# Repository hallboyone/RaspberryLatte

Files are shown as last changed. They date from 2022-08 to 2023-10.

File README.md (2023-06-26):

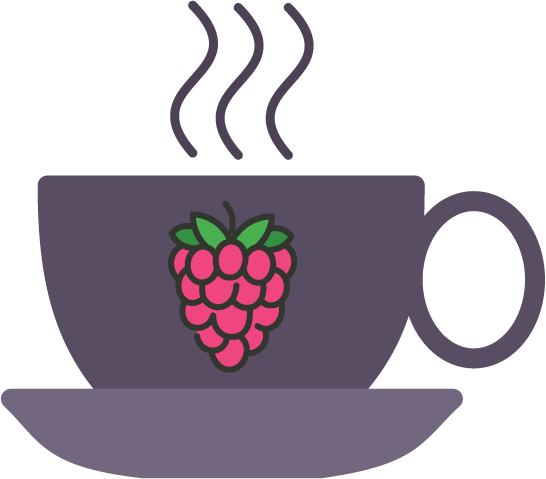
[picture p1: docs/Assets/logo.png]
#  RaspberryLatte 

A full stack suite to add smarts to a single boiler espresso machine using a Raspberry Pi Pico as the brains. The project was started with the following goals in mind:
- **Feature Rich:** Going beyond the standard PID temperature control, RaspberryLatte should provide advanced features that make pulling the perfect shot easier. These include
  - PID temperature control with feedforward components
  - Automatic flow control
  - Output scale
  - Preinfusion and autobrew routines
  - Coffee profiles
  - Scheduled heating *[Planned]*
  - Realtime state viewer (mobile UI) *[Planned]*
  - Machine statistic tracking *[Planned]*
  - Shot diagnosis and logging  *[Planned]*
- **Low Cost:** The cost should be minimized. The base hardware should be less than $100.
- **Discreet Appearance:** External parts, which would typically be 3D printed, should be minimized. Furthermore, the design should not require any external displays. In other words, the finished product should be discreet and not *look* like a DIY IoT device. 

## Features
### Advanced Temperature Control
Uses a PID controller with a feed-forward component to regulate the boiler's temperature. The resulting temperature is within 1% the setpoint throughout the shot.
<p align="center">
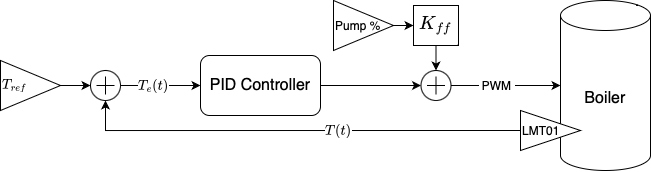
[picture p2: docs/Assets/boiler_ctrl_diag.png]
  
</p>

### Autobrew Routines with Flow Control
Automatically runs user configured brew routines. These will regulate the pump's power so that a desired flow rate is maintained over the course of the shot.

<p align="center">
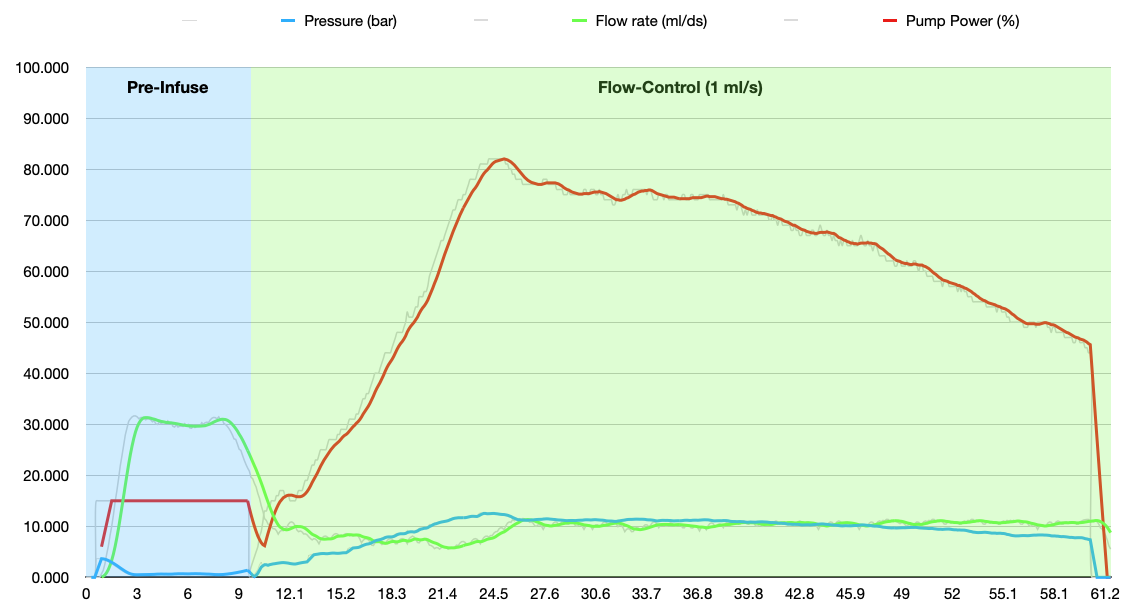
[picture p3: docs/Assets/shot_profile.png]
  
</p>

### User Adjustable Settings
The temperatures, flow rate, preinfusion routine, dose, yield, and other settings can all be customized without reflashing the code. The pump switch and mode dial are used to navigate a folder structure while the three LEDs display the current values of the parameters as they are adjusted. This allowed for full customization without any additional hardware (e.g. screens, buttons, etc.). 

## Project Architecture 

This project can be thought of in several layers. 
### Hardware Level
The lowest level is the hardware such as sensors and switches required to create a smart espresso machine. Additionally, a custom carrier board is needed to interface with these components. This PCB contains any circuitry required to support the sensors and switches. Mounted to this carrier board is the Raspberry Pi Pico W.
| Front View | Back View |
| --- | --- |
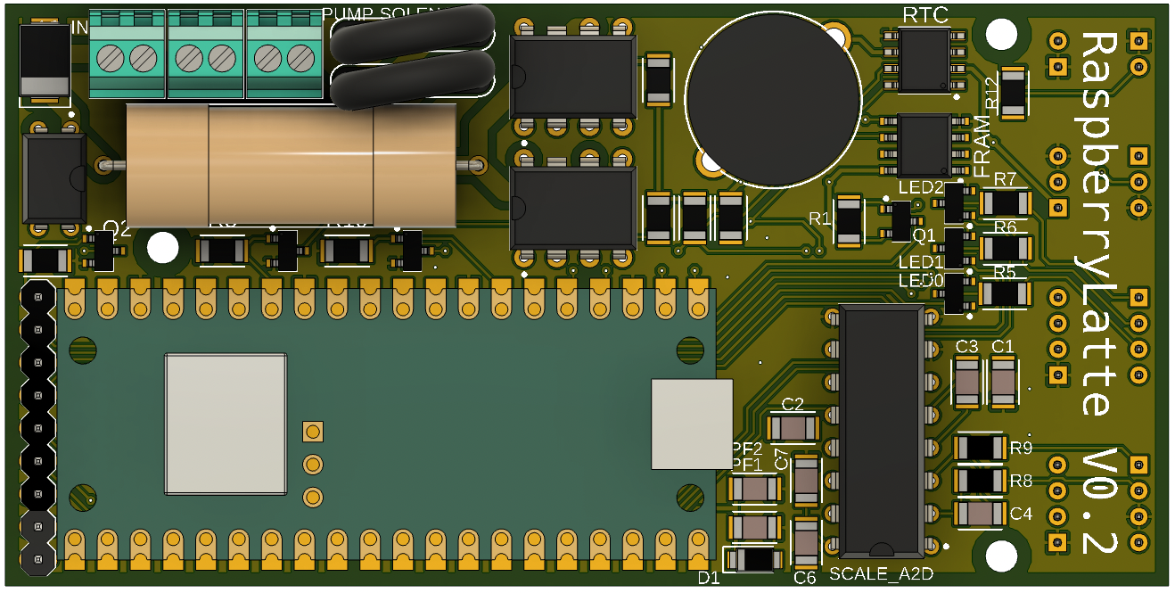
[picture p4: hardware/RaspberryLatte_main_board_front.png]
Front view of main board
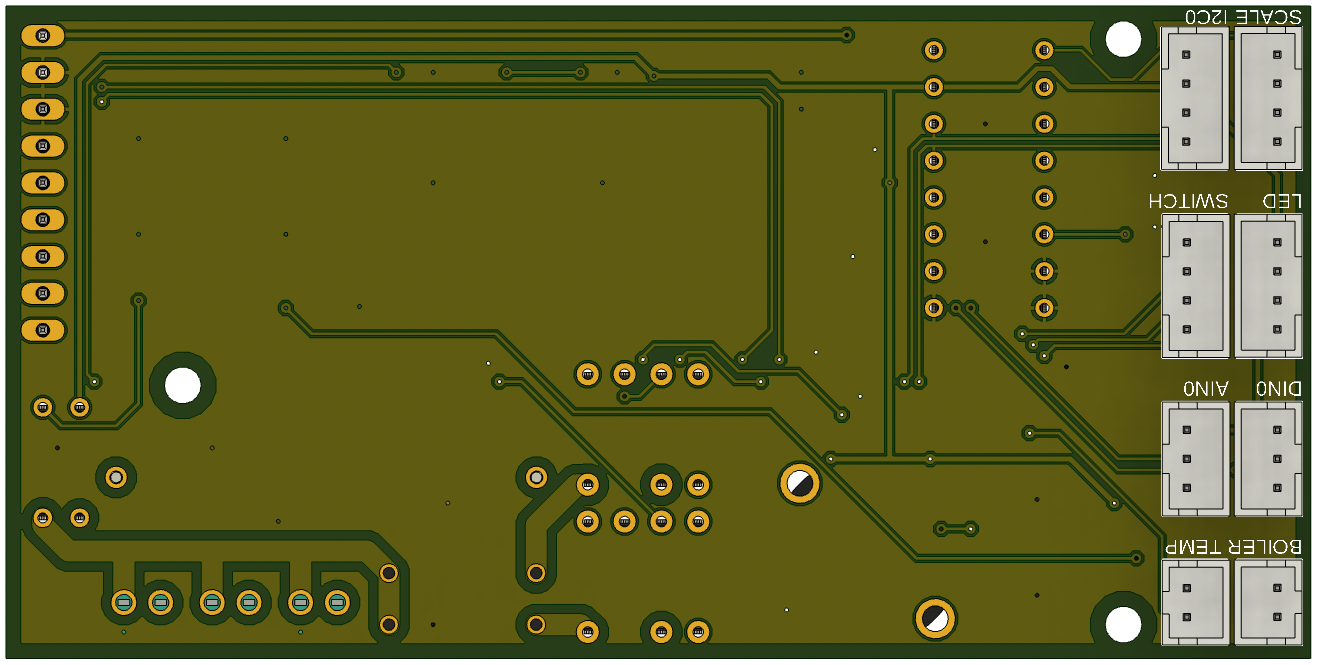
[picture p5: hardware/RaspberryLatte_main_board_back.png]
Back view of main board
 | 

### Firmware Level
The next level consists of the firmware running on the Pico. This code, written in c, contains all the sensor drivers and machine logic. The firmware is partitioned onto a single core of the dual core Pico.
### Network Level (Planned)
The network level runs on the second core on the Pico. It collects information from the firmware running on core 0 and shares that over BLE with the Mobile UI level (see below). It also passes settings received from a BLE client to the firmware so that the machines performance can be tailored to achieve the desired brew characteristics.
### Mobile UI Level (Planned)
While ssh is fun, a mobile application would be significantly more convenient. This level would allow users to create and share their brew profiles for different coffees, visualize a shot's flow rate, pressure, temperature, etc. in real time, and troubleshoot their shots. This application would interface with the Network level using BLE, simplifying the connection process.

## To-Do
- [x] Add carrier board design to repository
- [x] Add UI based on onboard switches and LEDs
- [x] Add flow control to autobrew routines
- [ ] Add wiring diagram
- [ ] Add BOM for hardware
- [ ] Implement network leve
- [ ] Implement mobile UI level
- [x] Design logo
- [ ] Write project documentation

## Documentation
### Project Documentation (Under Construction)
To help with your build, project documentation is being written in another [repository](https://github.com/hallboyone/RaspberryLatte-docs). Clone and build the sphinx docs to view.
<p align="center">
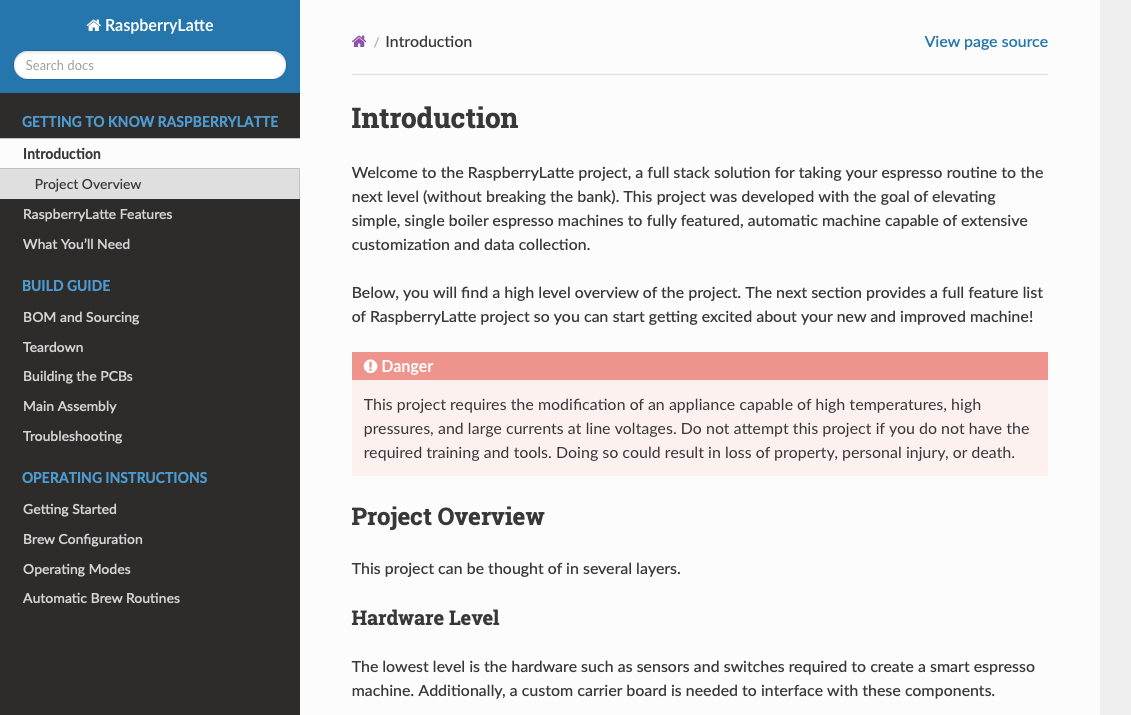
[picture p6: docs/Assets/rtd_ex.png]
RTD Documentation screenshot
  
</p>

### Code Documentation
The documentation is generated from the code's comments using doxygen. Below is a sample page showing the autobrew library. Clone and build the html to view the rest.
<p align="center">
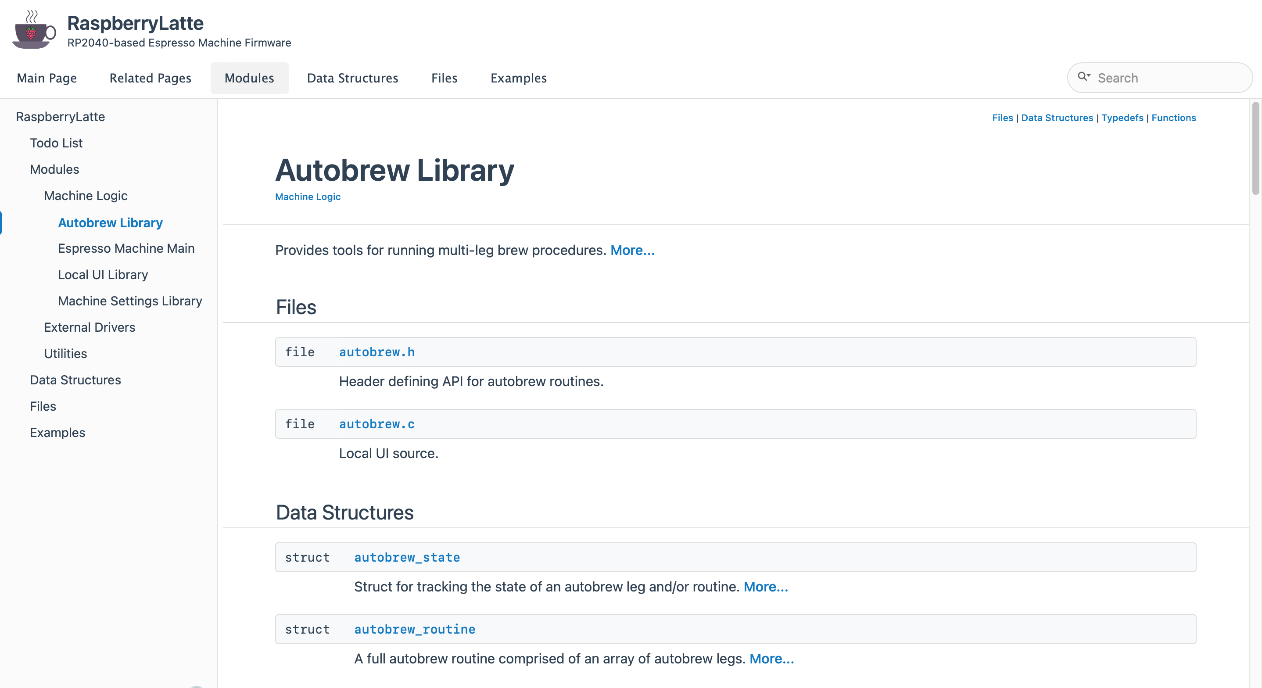
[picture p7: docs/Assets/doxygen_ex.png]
Doxygen screenshot
  
</p>

## Inspiration
This project has taken inspiration from others who have taken the time to write up their own builds. The two primary sources have been the [Es(pi)resso project](https://home-automations.net/project-coffee-espiresso-machine/), and the [Espresso for Geeks blog](https://www.instructables.com/Espresso-for-Geeks/). Big thank you to both those makers for sharing the great work they did!

## Contribute
If you are interested in helping with this project, I would love to talk! You can reach me through [Twitter](https://twitter.com/hallboyone "Richard Hall").

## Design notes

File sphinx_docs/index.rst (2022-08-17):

.. RaspberryLatte documentation master file, created by
   sphinx-quickstart on Tue Aug 16 21:35:44 2022.
   You can adapt this file completely to your liking, but it should at least
   contain the root `toctree` directive.

Welcome to RaspberryLatte's documentation!
==========================================

.. toctree::
   :maxdepth: 2
   :caption: Contents:

Indices and tables
==================

* :ref:`genindex`
* :ref:`modindex`
* :ref:`search`

Docs
====
.. doxygenfile:: autobrew.h

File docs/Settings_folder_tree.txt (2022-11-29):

0. Root (ooo)
    0.1. Settings (oox)
        0.1.1 Temp (oxo)
            0.1.1.1 Brew  [-1, 0.1, 1]
            0.1.1.2 Hot   [-1, 0.1, 1]
            0.1.1.3 Steam [-1, 0.1, 1]
        0.1.2 Weight (oxx)
            0.1.2.1 Dose  [-1, 0.1, 1]
            0.1.2.2 Yield [-1, 0.1, 1]
        0.1.3 More (xoo)
            0.1.3.1 Power (xox)
                0.1.2.1.1 Brew [-10, 1, 10]
                0.1.2.1.2 Hot  [-10, 1, 10]
            0.1.3.2 Preinf (xxo)
                0.1.3.2.1 On time  [-1, 0.1, 1]
                0.1.3.2.2 On power [-10, 1, 10]
                0.1.3.2.3 Off time [-1, 0.1, 1]
            0.1.3.3 Misc (xxx)
                0.1.3.3.1 Timeout   [-10, 1, 10]
                0.1.3.3.2 Ramp time [-1, 0.1, 1]
    0.2 Profiles (oxo)
        0.2.1 Profiles 1-3 (oxx)
            0.2.1.1 Profile 1 (xoo) [Save, Load, ~]
            0.2.1.2 Profile 2 (xox) [Save, Load, ~]
            0.2.1.3 Profile 3 (xxo) [Save, Load, ~]
        0.2.2 Profile 4-6 (xoo)
            0.2.2.1 xox Profile 4 (xox) [Save, Load, ~]
            0.2.2.2 xxo Profile 5 (xxo) [Save, Load, ~]
            0.2.2.3 xxx Profile 6 (xxx) [Save, Load, ~]
        0.2.3 Profile 7-9 (xox)
            0.2.3.1 xxo Profile 7 (xxo) [Save, Load, ~]
            0.2.3.2 xxx Profile 8 (xxx) [Save, Load, ~]
            0.2.3.3 ooo Profile 9 (ooo) [Save, Load, ~]

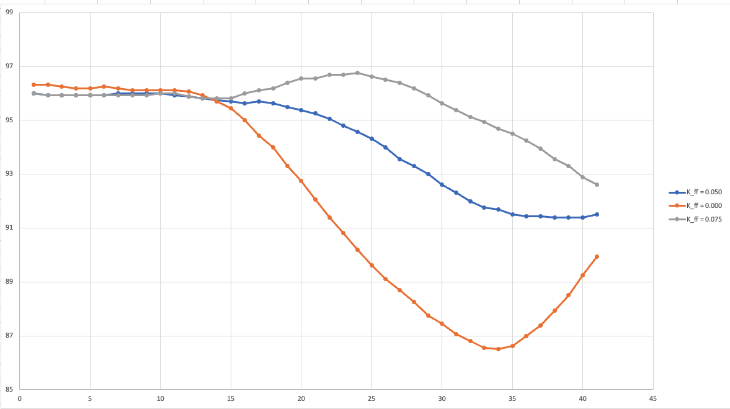
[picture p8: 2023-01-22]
docs/ff_comparison.png

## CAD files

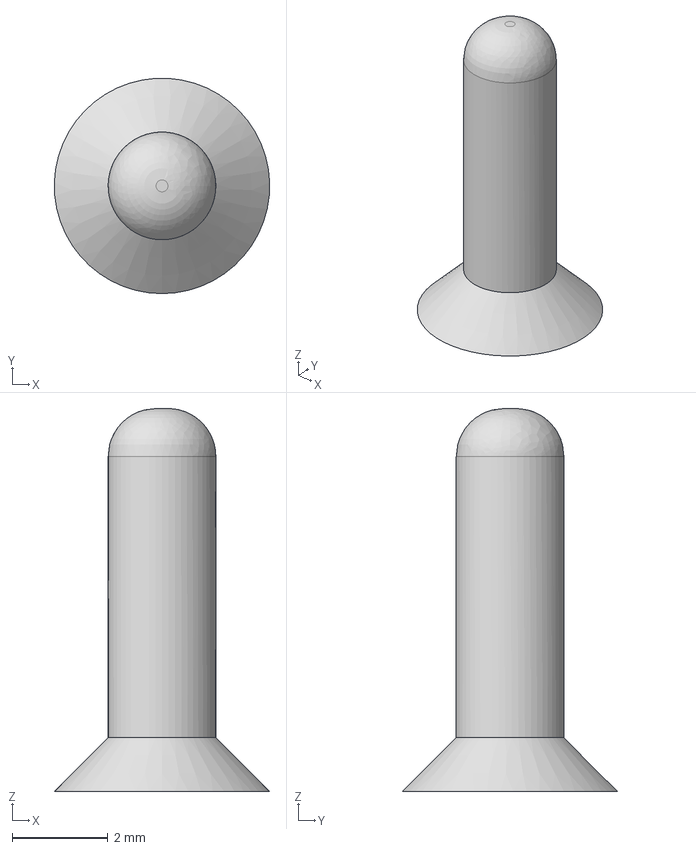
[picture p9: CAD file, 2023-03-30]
hardware/solid_models/main_board_pin.step
4.50 x 4.50 x 8.00 mm

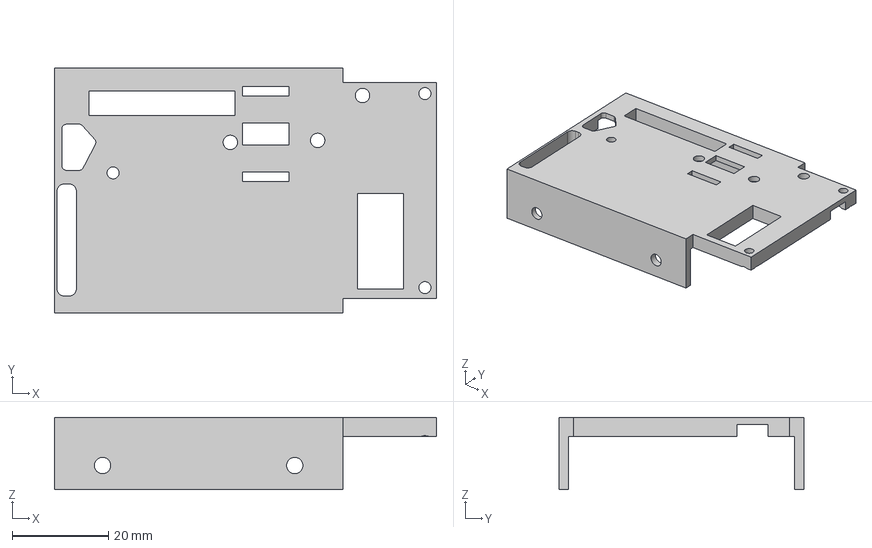
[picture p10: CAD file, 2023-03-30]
hardware/solid_models/main_board_mount.step
79.5 x 51.0 x 15.0 mm

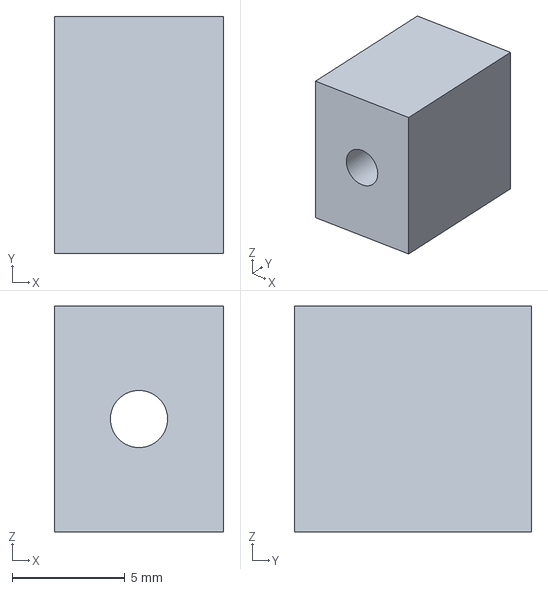
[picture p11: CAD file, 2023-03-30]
hardware/solid_models/led_board_mount.step
7.50 x 10.5 x 10.0 mm

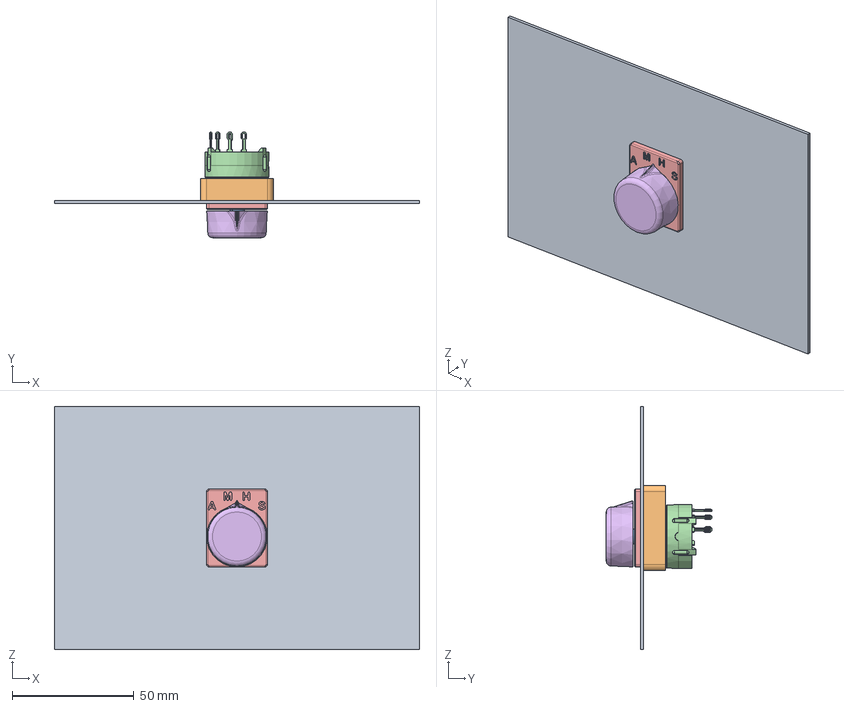
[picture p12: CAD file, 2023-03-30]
hardware/solid_models/mode_dial.step
150.0 x 43.4 x 100.0 mm
Switch_face
Clamp_back
Clamp_front
Knob

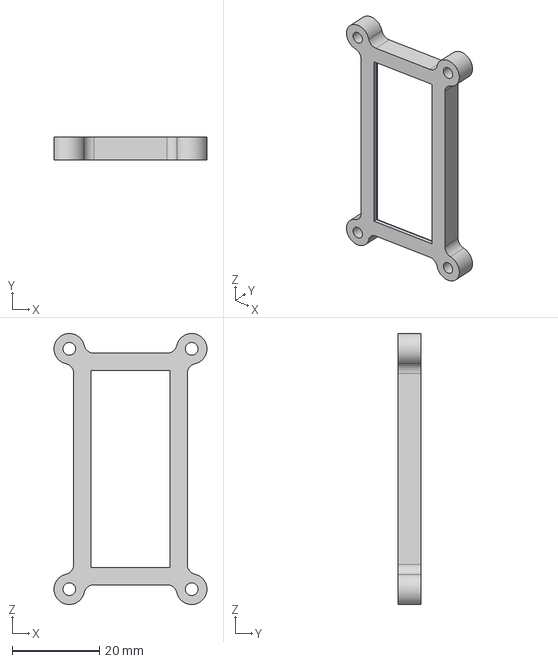
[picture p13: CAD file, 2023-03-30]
hardware/solid_models/power_supply_mount.step
35.0 x 5.25 x 62.0 mm

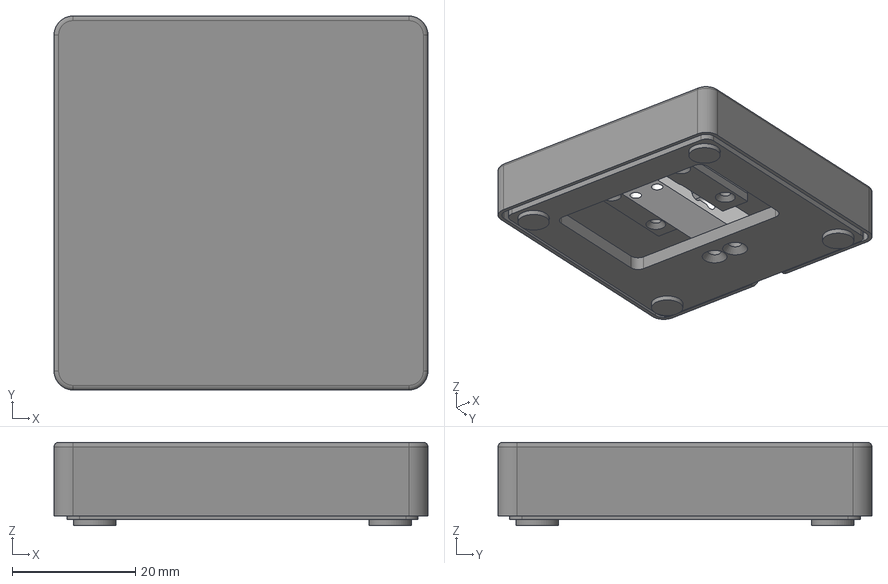
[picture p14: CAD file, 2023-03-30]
hardware/solid_models/espresso_scale.step
60.7 x 60.7 x 13.6 mm
Load cell
scale_base
scale_top_mount
scale_top
foot x 4

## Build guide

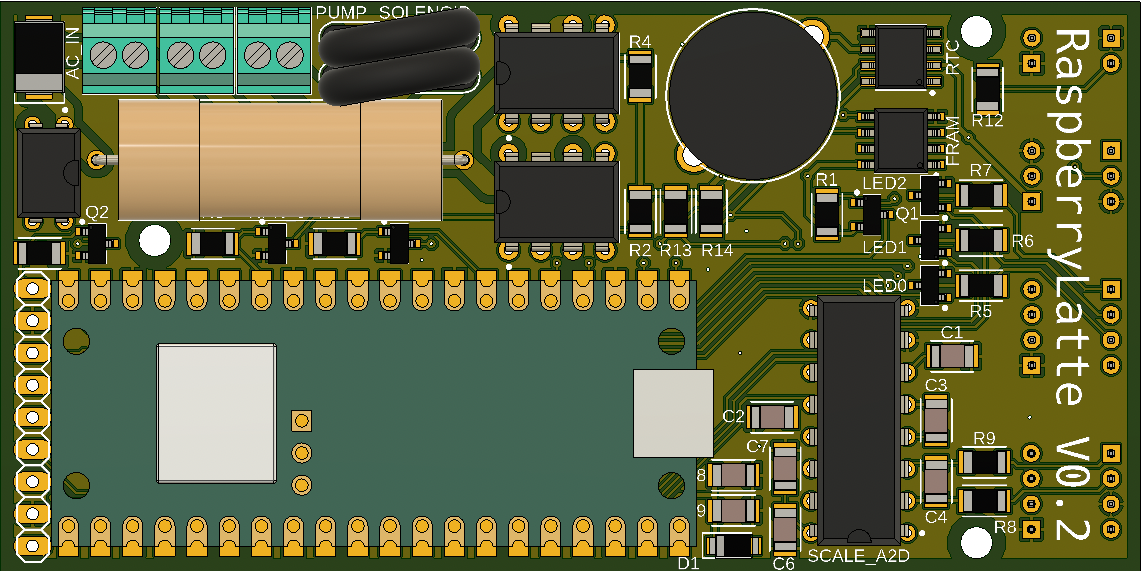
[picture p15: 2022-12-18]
docs/Wiring_diagram/main_board.png

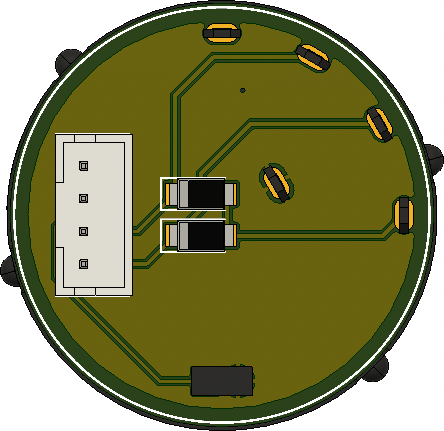
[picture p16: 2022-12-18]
docs/Wiring_diagram/dial_board.png

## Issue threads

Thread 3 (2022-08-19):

Missing I2C pull up resisters

hallboyone, 2022-08-19:
## Problem Summary
There is a note in section 4.3.1.3 of the RP2040 data sheet discussing the use of the RP2040's I2C hardware. It reads
> Note: There should also be external pull-ups on the board as the internal pad pull-ups may not be strong enough to pull up external circuits.

However, the current schematic relies on the internal pull-ups. This could be the cause of the intermittent problems communicating with the NAU7802.

## Proposed Solution
Add 4.7KOhm pull up resisters to the SDA and SCL lines on the RaspberryLatte main board.

hallboyone, 2022-10-05:
Fixed with new version of main board

Closed 2022-10-05.

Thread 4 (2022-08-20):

No external pull-up/pull-down resisters on board

hallboyone, 2022-08-20:
## Problem Summary
There are no external pull resisters on any of the main board's output signals (include the I2C bus as stated in #3). This can lead to dangerous situations where a crashed program and floating output can cause one of the AC components (heater, pump, solenoid) to get stuck in the on position.

## Proposed Solution
Add 4.7KΩ pull up resisters to all the output signal lines on the RaspberryLatte main board.

hallboyone, 2022-10-05:
Fixed with new version of main board

Closed 2022-10-05.

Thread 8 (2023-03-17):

Flow rate starts at non-zero value when machine is switched on.

hallboyone, 2023-03-17:
Probably something is not being reset correctly.

hallboyone, 2023-03-18:
After a little testing, the problem has been traced to noise in the flow sensor's power supply when the machine is switched on. This is read as a pulse by the pico. I tried a software fix (zeroing the flow sensor when the machine is powered on), but this led to corner cases where the sensor would be zeroed and then pulsed, leading to an occasional very large spike. It will be best to just clean the 5V power in the next version of the PCB. Until then, there will be some phantom flow rate now and then when the machine is turned on.

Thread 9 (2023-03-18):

Ground plan around AC traces

hallboyone, 2023-03-18:
There is not enough clearance around the traces caring AC loads on the PCB. The ground plan should be carved out in this area.

hallboyone, 2023-05-05:
Working on next version of PCB that fixes this.
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

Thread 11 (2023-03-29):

5V flow rate not supported by control board without modifications

hallboyone, 2023-03-29:
The control board was designed for 3.3V flow sensors. Turns out, they are almost exclusively 5V. To get around this with the current design, a jumper has to be soldered on and a voltage divider used to drop the 5V signal down to 3V. This should be updated in the next version of the board so no jumpers are needed. This is also related to issue #8 discussing cleaning the power to the flow sensor.

hallboyone, 2023-05-05:
I'm working on an update for the PCB that addresses this.
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

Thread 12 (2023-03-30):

Make integral windup bound dependent on output limits.

hallboyone, 2023-03-30:
Currently, the integral windup bound is set to a fixed value. However, this can lead to overshoot e.g. during flow control when 100% power is needed to reach the target flow rate. This leads to `e(t)*Kp + e_sum(t)*Ki = e(t)*Kp + 100 > 100` (where the last inequality holds only when the flow is below the target).

 Instead of the fixed bounds, `e_sum_lb <= e_sum(t) <= e_sum_ub`, the windup bound on the integral term should dependent on the proportional  input: `e_sum_lb - e(t)Kp <= e_sum(t) <= e_sum_ub - e(t)*Kp`. This is equivalent to the fixed bounds when at the set point, but it keeps prevents the error sum from growing when the error is large (i.e. the proportion term is dominate).

Closed 2023-03-30.

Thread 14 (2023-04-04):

Add pressure profiling to autobrew routines

hallboyone, 2023-04-04:
Currently, the auto brew routine can only regulate the flow rate. It is possible that the user may want to regulate the pressure instead. This should be added as an option for the auto brew routine.

Closed 2023-07-03.

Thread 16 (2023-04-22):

CRITICAL - Occasional erratic behavior in boiler

hallboyone, 2023-04-22:
I have observed occasional erratic behavior in the boiler. I'm not sure if it's software (sensor driver, PID implementation, etc) or hardware (sensor failure). Best guess is an overflow error somewhere in the PID controller, but I need to do more tests.

hallboyone, 2023-04-23:
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
After some testing, I think the problem is with the LMT01 sensor. For a single reading, the sensor will begin to report a temp around -50C, and the controller responds as it should. If these misreadings happen with increased frequency, the temperature will begin to increase and display the behavior I have observed.

Regardless of why we are getting bad readings, additional safe guards are needed to catch and stop this failure. Perhaps an error triggered by large differences between two temp readings. This should disable the boiler at the very least.

hallboyone, 2023-04-26:
While the sensor bug should definitely be addressed at some point, I think more important is the development of a boiler malfunction monitor within the code. I'll be opening a new issue to address it.

hallboyone, 2023-06-20:
After further thought, I think a median filter should be applied to the LMT01 sensor. This will reject the periodic spikes in its readings. The thermal runaway is triggered to throw an error if the temp reading varies too quickly so a spike will trip it (even if behavior returns to normal at the next reading). A median filter should fix this while only delaying the detection of a true problem by a couple hundred ms at most.

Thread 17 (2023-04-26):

Add thermal runaway safeguards

hallboyone, 2023-04-26:
There is currently nothing checking that the boiler is responding as expected to the heater inputs. This can lead to thermal runaways should the sensor come detached or fail. Functionality should be added to monitor the state of the boiler and enter an error state should a thermal runaway be sensed.
This could be modeled after the thermal runaway logic in the Marlin 3D printer firmware. The basic rules are
1.  The temp must be changing at some minimum rate when the machine is settling to a temperature (i.e. responding to control inputs)
2. The temp must not deviate too far from the setpoint after settling (i.e. sensor fails as in #16)

Closed 2023-05-04.

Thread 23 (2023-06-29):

Replace return-to-root with up-a-level in local_ui

hallboyone, 2023-06-29:
Currently, once you are don't changing a setting using the local_ui, you have to return to root before changing another setting. This is very annoying and would be better replaced with just going up a single level to the parent folder.

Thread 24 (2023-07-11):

ENHANCEMENT-update-settings-in-terminal

hallboyone, 2023-07-11:
Using the local dial and pump switch, though functional, is very clunky. With the newly expanded setting structure (120 folders!) it takes a long time to navigate and get set the way you want it. It would be much easier to do this with a console interface prior to the implementation of a remote application.

hallboyone, 2023-07-11:
This ended up being a bigger project than the original scope. The settings are now displayed as
```
Brew Temp   :  92.0 C
Hot Temp    : 100.0 C
Steam Temp  : 140.0 C
Dose        :  16.0 g
Yield       :  30.0 g
Brew Power  :   100 %
Hot Power   :    20 %

|=|=========================|========================|=========|
| |        Setpoint         |         Target         | Timeout |
|#|  Style  : Start :  End  | Flow : Pressure : Mass |         |
|-|---------:-------:-------|------:----------:------|---------|
|0|  Power  :   100 :   100 | 0.50 :    1.0   : 10.0 |  30.0   |
|1|  Flow   :  0.25 :  0.25 | 0.00 :    0.0   :  0.0 |   0.0   |
|2| Pressure:   2.5 :   2.5 | 0.00 :    0.0   :  0.0 |   0.0   |
|3|  Power  :    25 :    25 | 0.00 :    0.0   :  0.0 |   0.0   |
|4|  Power  :    25 :    25 | 0.00 :    0.0   :  0.0 |   0.0   |
|5|  Power  :    25 :    25 | 0.00 :    0.0   :  0.0 |   0.0   |
|6|  Power  :    25 :    25 | 0.00 :    0.0   :  0.0 |   0.0   |
|7|  Power  :    25 :    25 | 0.00 :    0.0   :  0.0 |   0.0   |
|8|  Power  :    25 :    25 | 0.00 :    0.0   :  0.0 |   0.0   |
|=|=========================|========================|=========|

RaspberryLatte
 (1) Settings
 (2) Autobrew
 (3) Presets
```
This is much cleaner than it was and should maintain it's format during use without needing to reprint everything with each change.

The settings can be navigated while the machine is off using "1"-"3" for subfolder selection, "u" to go up a level, "r" to go to root, and "p" to reprint (e.g. after resizing the terminal window).

Closed 2023-07-11.

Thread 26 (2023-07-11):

Flow rate sensor is slow and not accurate at low flows

hallboyone, 2023-07-11:
It could be replaced with something like [this](https://www.alibaba.com/product-detail/EPT-small-size-output-water-flow_1600425267625.html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). However, this will require retuning everything, but this is probably okay since the flow control never worked great anyway.

hallboyone, 2023-07-12:
I'm testing a new sensor (linked above) and have collected the following data.
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
The slope of the trend line is the conversion between the pulses and volume. The exact values to 6 decimal places are
```
slope     =  0.009472
intercept = -0.054317
```

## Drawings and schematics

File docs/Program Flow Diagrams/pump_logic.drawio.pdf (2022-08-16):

## Espresso Machine Pump Logic

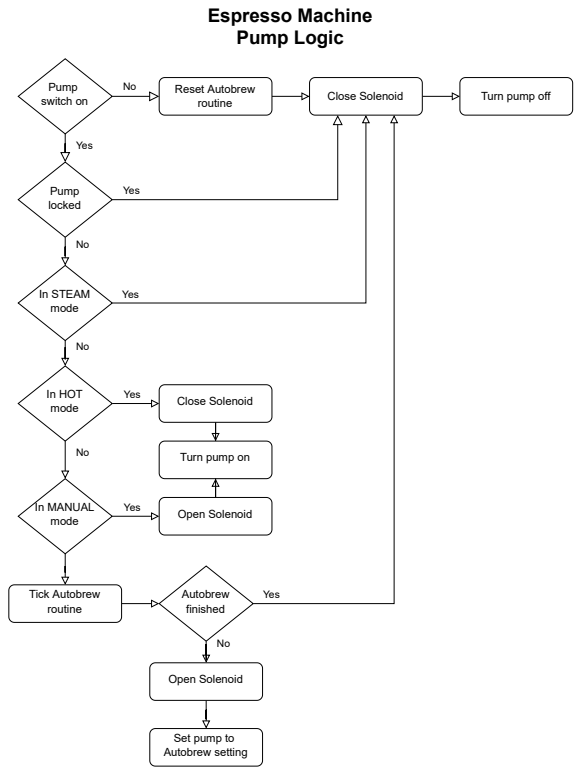
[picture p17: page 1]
Yes; Pump; switch on; Reset Autobrew routine; Pump locked; Close Solenoid; Turn pump off; In STEAM mode; In HOT; mode; In MANUAL; Open Solenoid; Tick Autobrew routine; Autobrew; finished

Turn pump on

Set pump to
Autobrew setting

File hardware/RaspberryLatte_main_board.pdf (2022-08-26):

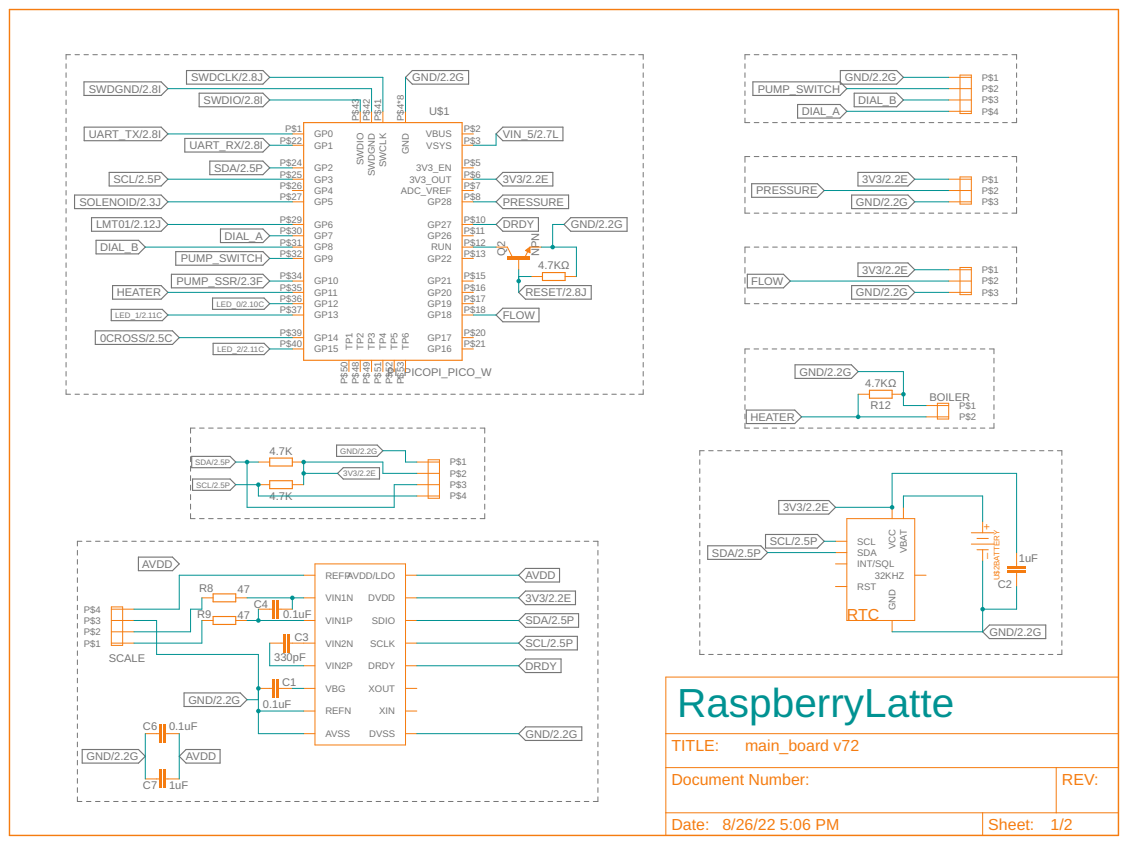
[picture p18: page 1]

Document Number: | REV:

Date: 8/26/22 5:06 PM | Sheet: 1/2

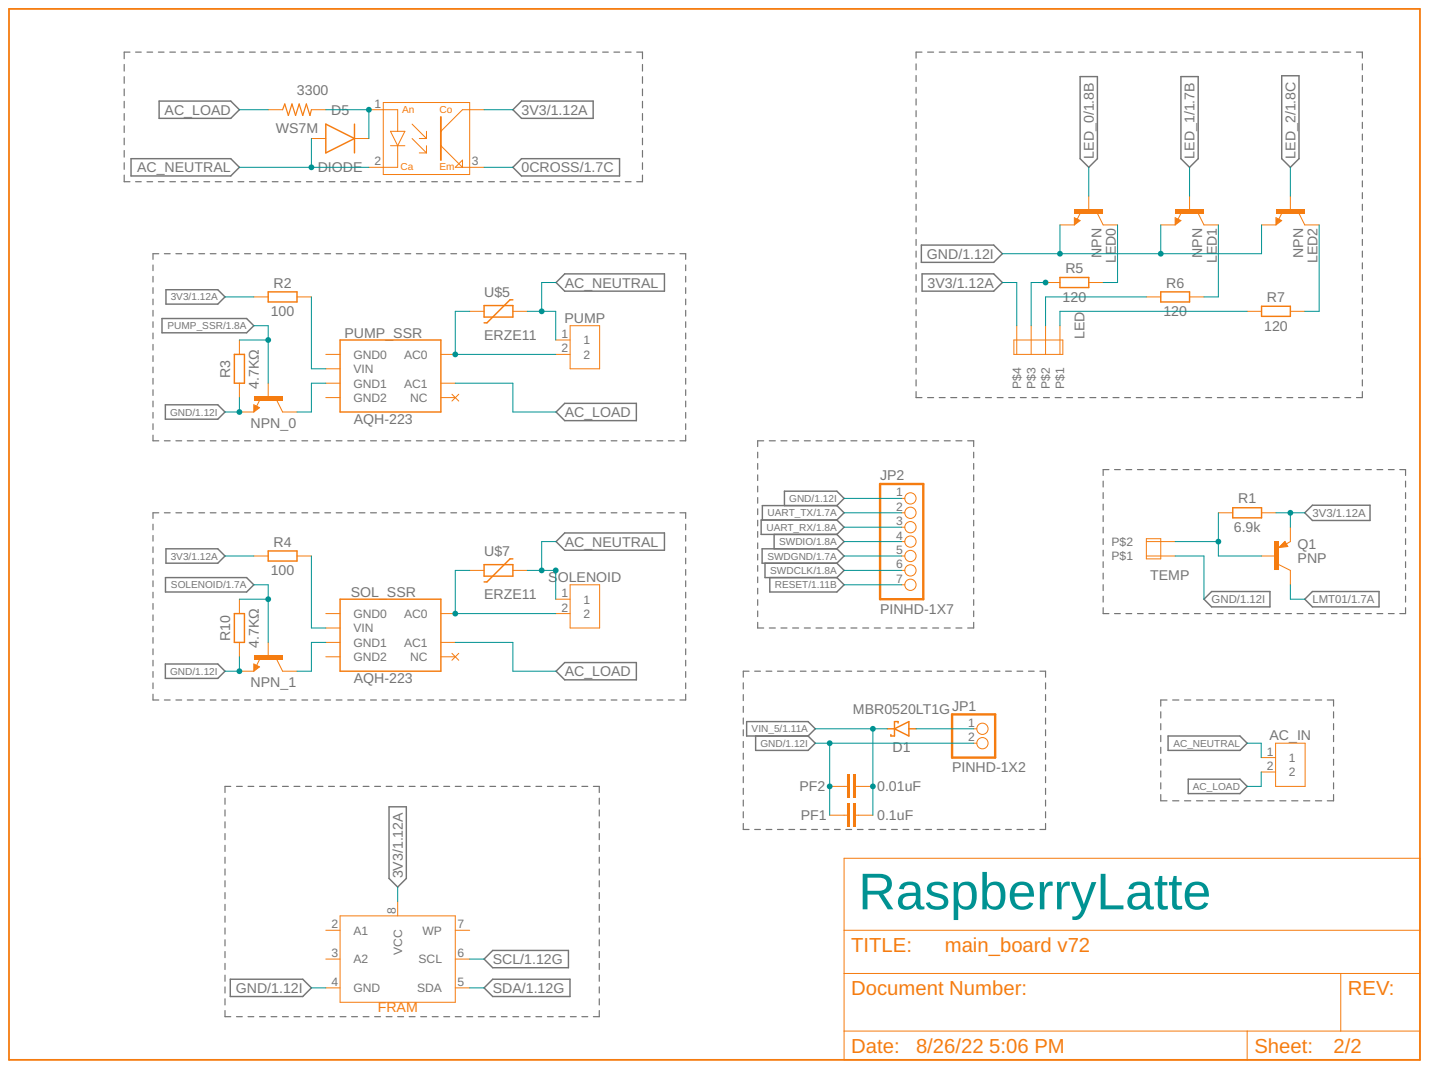
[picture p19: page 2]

Document Number: | REV:

Date: 8/26/22 5:06 PM | Sheet: 2/2

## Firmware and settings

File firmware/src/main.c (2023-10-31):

#define PRINT_MACHINE_STATUS_OVER_UART

#ifdef PRINT_MACHINE_STATUS_OVER_UART
#include <stdio.h>
#endif

#include "machine_logic/espresso_machine.h"

int main(){
    // Setup UART
    stdio_uart_init_full(PICO_DEFAULT_UART_INSTANCE, 115200, PICO_DEFAULT_UART_TX_PIN, PICO_DEFAULT_UART_RX_PIN);

    espresso_machine_viewer espresso_machine;
    if(espresso_machine_setup(&espresso_machine)) return 1;

    // Loop rate limiter
    absolute_time_t next_loop_time = get_absolute_time();
    const uint64_t loop_period_ms = 10;

    #ifdef PRINT_MACHINE_STATUS_OVER_UART
    const uint16_t ticks_per_message = 20;
    uint32_t num_ticks = 0;
    #endif

    while(true){
        next_loop_time = delayed_by_ms(next_loop_time, loop_period_ms);

        #ifdef PRINT_MACHINE_STATUS_OVER_UART
        num_ticks += 1;
        // Print status periodically 
        if(num_ticks%ticks_per_message == 0){
            if(espresso_machine->switches.ac_switch){
                printf("%5.1f\t%5.1f\t%3d\t%2d\t%3d\t%5.2f\t%4.1f\t%d\n",
                espresso_machine->boiler.setpoint/100.,
                espresso_machine->boiler.temperature/100.,
                espresso_machine->boiler.power_level,
                espresso_machine->autobrew_leg,
                espresso_machine->pump.power_level,
                espresso_machine->pump.flowrate_ml_s,
                espresso_machine->pump.pressure_bar,
                espresso_machine->scale.val_mg);
            }
        }
        #endif

        // Update the machine
        espresso_machine_tick();

        sleep_until(next_loop_time);
    }
}

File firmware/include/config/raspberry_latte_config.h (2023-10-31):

/**
 * Length of time after powering on that the boiler and pump remain inactive. 
 * Let's transient voltages settle out before activating the machine.
 */
#define AC_SETTLING_TIME_MS 500

/** \brief The difference between the zerocross sense time and the actual zerocross time. */
#define AC_0CROSS_SHIFT 0

#define BOILER_PID_GAIN_P 0.05
#define BOILER_PID_GAIN_I 0.00000175
#define BOILER_PID_GAIN_D 0.0
#define BOILER_PID_GAIN_F 0.00005
#define FLOW_PID_GAIN_P   0.0125
#define FLOW_PID_GAIN_I   0.00004
#define FLOW_PID_GAIN_D   0.0
#define FLOW_PID_GAIN_F   0.0

#define SCALE_CONVERSION_MG -0.152710615479

/** ml per pulse of pump flow sensor. */
#define PULSE_TO_FLOW_CONVERSION_ML  0.009472

// Between two temp readings, the temperature must not change by more than this amount.
#define THERMAL_RUNAWAY_WATCHER_MAX_CONSECUTIVE_TEMP_CHANGE_cC 1000

// Defines the window over which a change in temperature must be observed while converging to setpoint.
#define THERMAL_RUNAWAY_WATCHER_MIN_TEMP_CHANGE_PERIOD_MS 20000
#define THERMAL_RUNAWAY_WATCHER_MIN_TEMP_CHANGE_HEAT_cC  200
#define THERMAL_RUNAWAY_WATCHER_MIN_TEMP_CHANGE_COOL_cC  100

// Defines how close to the setpoint counts as convergence and how far counts as divergence
#define THERMAL_RUNAWAY_WATCHER_CONVERGENCE_TOL_cC 100
#define THERMAL_RUNAWAY_WATCHER_DIVERGENCE_TOL_cC  800

#define PUMP_SWITCH_DEBOUNCE_DURATION_US 10000
#define MODE_DIAL_DEBOUNCE_DURATION_US 75000

#define AUTOBREW_PREINF_END_PRESSURE_MBAR 3000
#define AUTOBREW_BREW_PRESSURE_MBAR       9000

#define THERMAL_RUNAWAY_WATCHER_LED_TOGGLE_PERIOD_MS 512

/**
 * The temp that the thermometer is reading may not match the water at the group-head.
 * This constant defines the discrepancy. Compute the value in C and then multiply by 
 * 16 and round to an integer. 
*/
#define BOILER_TEMP_OFFSET_cC 800

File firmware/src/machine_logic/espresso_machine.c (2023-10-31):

/**
 * \file espresso_machine.c
 * \ingroup espresso_machine
 * \author Richard Hall (hallboyone@icloud.com)
 * \brief Espresso Machine source
 * \version 0.1
 * \date 2022-12-09
 */

//#define ENABLE_BOILER

#include "machine_logic/espresso_machine.h"

#include <stdio.h>

#include "config/raspberry_latte_config.h"
#include "config/pinout.h"

#include "machine_logic/autobrew.h"
#include "machine_logic/machine_settings.h"

#include "drivers/nau7802.h"
#include "drivers/lmt01.h"
#include "drivers/ulka_pump.h"

#include "utils/thermal_runaway_watcher.h"
#include "utils/gpio_irq_timestamp.h"
#include "utils/binary_output.h"
#include "utils/binary_input.h"
#include "utils/slow_pwm.h"
#include "utils/i2c_bus.h"
#include "utils/pid.h"
#include "utils/macros.h"

/** An internal variable that collects the current state of the machine. */
static espresso_machine_state _state = {.pump.pump_lock = true, .boiler.temperature = 0}; 

/** I2C bus connected to memory, scale ADC, and I2C port */
static i2c_inst_t *  bus = i2c1;
static thermal_runaway_watcher trw;         /**< Watches the boiler state to make sure it's behaving as expected. */
static binary_output           leds;        /**< The three LEDs indicating to the user the machine's state. */
static binary_input            pump_switch; /**< Monitors the state of the pump switch. */
static binary_input            mode_dial;   /**< Monitors the state of the mode dial. */
static absolute_time_t         ac_on_time;  /**< Records the time of when the machine was switched on. */
static binary_output           solenoid;    /**< Drives the digital output for the solenoid. */
static slow_pwm                heater;      /**< PWM signal for the SSR driving the boiler. */
static lmt01                   thermo;      /**< Boiler thermometer. */
static nau7802                 scale;       /**< Output scale. */
static ulka_pump               pump;        /**< The vibratory pump. */

/** Boiler controller */
static pid  heater_pid;
/** Flow controller */
static pid  flow_pid;                    

#ifdef ENABLE_BOILER
/** 
 * \brief Shuts down the pump and boiler. 
*/
static void espresso_machine_e_stop();
#endif

/**
 * \brief Checks if the AC is on.
 * If the last AC zerocross time was within 17,000us (a little over a 60hz 
 * period), then it's assumed on.
 * \return True AC is on. False otherwise.
 */
static inline bool is_ac_on(){
    return (gpio_irq_timestamp_read_duration_us(AC_0CROSS_PIN) < 17000);
}

/** 
 * \brief Checks if AC has settled.
 * The AC is assumed settled once AC_SETTLING_TIME_MS have passed and AC is on. 
 * The time should be long enough to allow transient spikes to die out. 
 * \return True if ac has settled. Else, returns false.
 */
static inline bool is_ac_on_and_settled(){
    return is_ac_on() && absolute_time_diff_us(ac_on_time, get_absolute_time()) > 1000*AC_SETTLING_TIME_MS;
}

/** 
 * \brief Getter for the boiler temp. 
 * Used as a helper function for the boiler PID controller.
 * \returns The current boiler temp in C. 
 */
static pid_data read_boiler_thermo_C(){
    return lmt01_read_float(thermo);
}

/** 
 * \brief Getter for the pump's flowrate. 
 * Used as a helper function for the pumps flow controller.
 * \returns The current flow rate through the pump in ul/s. 
 */
static pid_data read_pump_flowrate_ul_s(){
    return 1000.0*ulka_pump_get_flow_ml_s(pump);
}

/** 
 * \brief Setter for the boiler's duty cycle. 
 * Used as a helper function for the boiler PID controller.
 * \param u A duty cycle with 0 being off and 1 being full on.
 */
static void apply_boiler_input(float u){
    slow_pwm_set_float_duty(heater, u);
}

/** 
 * \brief Zeros the scale. 
 * Helper for autobrew routine.
 */
static void zero_scale(){
    nau7802_zero(scale);
}

/** 
 * \brief Resets flow control and sets the bias to the current pump power.
 * Helper for the autobrew routine.
 */
static void setup_flow_ctrl(){
    pid_reset(flow_pid);
    pid_update_bias(flow_pid, ulka_pump_get_pwr(pump));
}

/** 
 * \brief Checks if the scale is greater than or equal to the passed in value. 
 */
static bool scale_at_val(int32_t val_mg){
    return nau7802_at_val_mg(scale, val_mg);
}

/** 
 * \brief Checks if flowrate is greater than or equal to the passed in value. 
 */
static bool system_at_flow(int32_t flow_ul_s){
    if(flow_ul_s > 0){
        return 1000.0*ulka_pump_get_flow_ml_s(pump) >= flow_ul_s;
    } else {
        return 1000.0*ulka_pump_get_flow_ml_s(pump) <= -flow_ul_s;
    }
}

/** 
 * \brief Checks if pump has triggered target pressure.
 * 
 * If pressure is positive, then returns true if pressure is greater than target.
 * If pressure is negative, then returns true if pressure is less than target.
 */
static bool system_at_pressure(int32_t pressure_mbar){
    if(pressure_mbar > 0){
        return ulka_pump_get_pressure_bar(pump) >= (pressure_mbar/1000.);
    } else {
        return ulka_pump_get_pressure_bar(pump) <= -(pressure_mbar/1000.);
    }
}

/** 
 * \brief Returns the pump power required to hit target pressure (clipped between 0 and 100).
 * \param target_pressure_mbar The pressure in mbar that is targeted.
 * \returns The pump power needed to hit the target pressure in percent power.
*/
static uint8_t get_power_for_pressure(uint16_t target_pressure_mbar){
    return ulka_pump_pressure_to_power(pump, target_pressure_mbar/1000.0);
}

/** \brief Returns the pump power needed to regulated to the target flow rate.
 * 
 * The flow_ctrl PID object is updated to the new setpoint, ticked, and the current input is returned.
 * 
 * \param target_flow_ul_s The target flowrate in ul/s.
 * \returns The pump power needed to reach the target flowrate, according to the flow_ctrl PID object.
*/
static uint8_t get_power_for_flow(uint16_t target_flow_ul_s){
    pid_update_setpoint(flow_pid, target_flow_ul_s);
    return (uint8_t)pid_tick(flow_pid, NULL);
}
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

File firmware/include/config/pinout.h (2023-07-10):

/**
 * \file pinout.h
 * \author Richard Hall (hallboyone@icloud.com)
 * \brief Macros defining the pinout of the RaspberryLatte main board
 * \version 0.1
 * \date 2022-12-09
 */

#ifndef PINOUT_H
#define PINOUT_H

#define I2C_SDA_PIN           2 /**<\brief I2C data pin. */
#define I2C_SCL_PIN           3 /**<\brief I2C clock pin. */
#define SOLENOID_PIN          5 /**<\brief 3-way solenoid control pin. */
#define LMT01_DATA_PIN        6 /**<\brief LMT01 data pin. */
#define DIAL_A_PIN            7 /**<\brief Front dial pin A. */
#define DIAL_B_PIN            8 /**<\brief Front dial pin B. */
#define PUMP_SWITCH_PIN       9 /**<\brief Pump switch pin. */
#define PUMP_OUT_PIN         10 /**<\brief Pump control pin. */
#define HEATER_PWM_PIN       11 /**<\brief Boiler control pin. */
#define LED2_PIN             12 /**<\brief LED 2 control pin. */
#define LED1_PIN             13 /**<\brief LED 1 control pin. */
#define AC_0CROSS_PIN        14 /**<\brief Zerocross sensor pin. */
#define LED0_PIN             15 /**<\brief LED 0 control pin. */
#define FLOW_RATE_PIN        18 /**<\brief Flow rate data pin. */
#define PRESSURE_SENSOR_PIN  28 /**<\brief Analog pressure sensor pin. */
#endif

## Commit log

2022-01-30 Replaced phasecontrol configuartion on core1 with a struct.
    [main.c]
2022-02-08 Ran more tests. I think thermo is bad. Ordered TI LMT01. Going to write driver now.
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2022-02-22 Have a bit-banging solution for the lmt01 sensor. Trying to get the pio solution to work.
2022-02-22 Wrote a header for the physical inputs. It can stream data over UART but I need to make notes about its endiness.
2022-02-23 Added the code for the analog pressure sensor. Currently transmitting the raw result from the adc.
2022-02-23 Create pressure_transducer.txt
    Discusses the sensor used and the linear conversion from adc reading to bar.
2022-04-15 Added pin and pio config to HX711 struct
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2022-04-19 Working on uart_bridge. Have send and recieve written.
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2022-04-20 I have the pressure sensor attached to uart bridge!
2022-04-20 Restructured project
    Combining pi zero software with pi pico firmware.
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2022-04-22 Wrong name in main and added phasecontrol
    [main.c]
2022-04-27 Working on code for heater's low freq PWM
2022-04-28 Added 1ms delay when reading a message over UART.
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2022-05-05 Had heater attached to UART pin. Moved to GPIO 4
2022-05-05 Rewrote LMT01 driver to account for inverted pulses.
2022-05-05 Replaced UART timer with msg len check
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2022-05-08 Stupid bug. Used || instead of |
    [binary_input.c]
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2022-05-08 Added ability to call uart_bridge from cmd ln
2022-05-08 Added ac_hot bridge and fixed wrong handler
    [phasecontrol.c, pinout.h]
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2022-05-09 Wrote discrete derivative and integral classes for PID
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2022-05-10 Replaced 0.5s delay with increased uart timeout
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2022-05-11 binary_output required python script to know pico wiring or programing. Replaced with leds.
    [binary_output.c, main.c, pinout.h]
2022-05-11 Added reset function to PID
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2022-05-12 Fixed bug in reset function where leg index wasn't reset to 0
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2022-05-24 Rewriting getters in software using new uart_bridge structure.
2022-05-25 Reworked python uart_bridge. Message (un)packing now handled in component objects.
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2022-05-28 Made a logging object that can track the different parameters during autobrew
2022-06-11 Fixed bugs in uart_bridge.py
2022-06-11 Forgot self when calling parent function in Heater
2022-06-11 Forgot self when calling parent function in Pump
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2022-06-13 Called leds_set with gpio num instead of led index
2022-06-13 Replaced read with update in Switches
2022-06-13 Adjusted PID gains and using update method in Switches
2022-06-14 Improved error handling in binary_input.c
    [binary_input.c]
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2022-06-14 Updated UART to return a status with each transmission.
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2022-06-15 Updated pressure sensor to use new UART bridge
2022-06-16 bugfix: referece to renamed var in Heater
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2022-06-16 FEATURE: disable pump after dial change until switched off
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2022-06-21 Increased the logger sample time and removed extra sources
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2022-07-20 BUGFIX: Bad cast in heater
2022-07-21 Added files for Pico PID. Started in on discrete derivative.
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2022-07-22 Corrected I2C channel
2022-07-22 Added LED init that was deleted at some point.
2022-07-22 Finished scale UART bridge. In a working state.
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2022-07-27 Fixed some weirdness with the cyw43_arch related to gpio_put in ISR.
    [main.c]
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2022-07-28 Refactored binary input to use structs and added invert field.
    [binary_input.c]
2022-07-28 Updated main to use new binary inputs with invert
    [main.c]
2022-07-28 Added reset and UARTClear to start of EspressoMachine
2022-07-29 Updated. LED pinout was wrong.
    [pinout.h]
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2022-07-31 Updated the python LED class to use new binary_ouput sdk.
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2022-08-02 BUG < where there should have been a >=
    [binary_input.c]
2022-08-02 BUG UART handler used wrong message ID in response
    [binary_output.c]
2022-08-02 BUG Returned value over UART did not account for clipping
2022-08-02 BUG Phasecontrol dutycycle handler did not return value
    [phasecontrol.c]
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2022-08-02 REFACTOR Changed how uart_bridge.py worked. Easier to use.
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2022-08-02 Using LEDs 1 and 2 as debugging tools
2022-08-02 Decreased main loop rate to 20Hz from 100Hz
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2022-08-04 uart_bridge.py trys to resend after failure
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2022-08-08 Updated pressure to new bridge. Split id and len into seperate bytes.
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2022-08-08 Updated phasecontrol to new uart bridge. Major changes.
2022-08-08 Added solenoid to new bridge and deleted old files.
2022-08-08 Finished pico side of new bridge. Compiles but untested.
2022-08-09 Working on finishing bridge. Still several critical bugs.
    [binary_input.c, phasecontrol.c]
2022-08-09 Improved phasecontrol src. Trying to address major bugs
    [phasecontrol.c]
2022-08-09 Found a missing & in main. This may be my critical bug!
    [main.c]
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2022-08-09 Fixed critical bug where absolute time instead of delta time was used.
    [phasecontrol.c]
2022-08-10 Made pico vars global static. Moved power LED logic to pico.
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2022-08-11 Have autobrew working with just some small issues.
    [main.c]
2022-08-11 Bugfix (overflow error in autobrew) and code refactor (autobrew much cleaner).
    [main.c]
2022-08-12 Added pump lock and led logic. Improved pump logic.
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2022-08-12 Fixed a few critical bugs.
    [espresso_machine.c, main.c]
2022-08-13 Deleted lots of old files
    Entire python portion of project not needed anymore. Everything is moved onto the pico.
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2022-08-16 Added ability to switch between coffees in brew_parameters
2022-08-17 BUGFIX Misspelled function call
    [espresso_machine.c]
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2022-08-18 Fixed incorrect return value. Should have been void and saved to pointer.
    [i2c_bus.c]
2022-08-19 Wrong pinout for i2c
    [pinout.h]
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2022-08-19 Added error handleing and timeouts to NAU7802 driver
    [nau7802.c, nau7802.h]
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2022-09-02 Reorganized folders
    Removed brew log viewers. Added board archives and figures to hardware folder.
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2022-09-04 Moved heater to be the first thing init'd in espresso_machine
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2022-09-04 Added function to check if dev present on i2c bus
2022-09-04 Deleted hw setup fun in nau7802. It is replaced by i2c_bus
    [nau7802.c]
2022-09-05 Moved I2C bus setup into espress_machine since bus used in multiple components
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2022-09-21 Updated dial debounce len and switch invert
    [espresso_machine.c]
2022-09-23 Fixed a critical bug in i2c_bus_write_bytes
    [i2c_bus.c, nau7802.c]
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2022-10-06 Changed some consts to defines to fix compile problem on pi 4
    [nau7802.c]
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2022-10-15 Added ff term tying flowrate to heater setting during autobrew.
2022-10-16 Fixed spelling mistakes
    It's temperature, not tempurature.
    [espresso_machine.c, main.c]
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2022-10-20 Fixed bug where multi byte regester addresses where sent backwards over I2C
    [i2c_bus.c]
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2022-10-20 Updated mb85_fram function to read IC capacity.
    It should be faster now.
2022-10-20 Dramatically reduced the time to compute FRAM capacity.
2022-10-21 Added value_flasher for displaying values with LEDs. Tested but undocumented.
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2022-11-01 Trying to test current config. Debug toolchain not working.
    [espresso_machine.c, main.c]
2022-11-01 Fixed bug related to settings array and added enter_settings state to e.m.
    [espresso_machine.c, main.c]
2022-11-01 hotfix - Pump lock not engaged when machine turned on
2022-11-07 Debug print statements and fu checking if folder is action
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2022-11-07 Added hot power, full setting adjustment, and autobrew refresh
2022-11-09 Fixed a few bugs. printing wrong thing, && instead of &
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2022-11-11 Reworked how the settings worked. Moved UI into machine_settings. Untested.
    [espresso_machine.c]
2022-11-11 Early testing. Found some critical bugs
    [espresso_machine.c]
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2022-11-15 Converting pump powers from percentage to actual power.
2022-11-15 Bug in debugging print statement
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2022-11-18 Fixed bug in autobrew setup
    [espresso_machine.c]
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2022-12-12 Using wrong loop period in main
    [main.c]
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2022-12-18 No longer return sum and slope values when adding point to integral and derivative
    [espresso_machine.c]
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2022-12-23 Increased flow meter's filter span. Adds new dp on read.
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2022-12-23 Using flow_sensor in espresso machine for ff boiler ctrl
2022-12-23 Reverted main to development branch
    [main.c]
2022-12-23 Added feedforward plots
    [ff_comp.xlsx]
2023-01-22 Added computation of pressure
    Used to turn down pump is pressure gets too high.
    [espresso_machine.c, main.c]
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2023-01-25 Adding zerocross_timer lib
    This will pull the zerocross logic out of phasecontrol. This will separate the AC power status from the pump logic.
2023-01-26 Replaced zerocross_timer with general gpio_irq_timestamp
    [gpio_irq_timestamp.c]
2023-01-26 Using logic local to e-machine to check if AC is hot
    This will allow additional abstraction of the pump in a way that makes sense (it would have been weird to ask the pump library if the AC is hot).
2023-01-29 Fixed breaking bugs in GPIO utils
    [gpio_irq_timestamp.c, gpio_multi_callback.c]
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2023-02-05 Updated PID API to match rest of firmware
2023-02-05 Changed print condition in main to AC switch on
2023-02-05 Fixed bug in pump lib
2023-02-06 Fixed bug in autobrew setup fun
    [espresso_machine.c]
2023-02-12 Increased the flow meter's filter range from 0.5 to 1.5s
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2023-02-16 Update autobrew docs to reflect percent power use.
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2023-02-22 Issues in discrete derivative. Not working
    [espresso_machine.c, flow_meter.c, main.c]
2023-02-28 Continued work on pid (float to int, docs, clean, etc.)
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2023-03-04 Added missing return statement.
    [gpio_multi_callback.c]
2023-03-04 Fixed bugs in flow_meter and added deinit fun
    [flow_meter.c]
2023-03-12 Still working on reducing floating point errors
    [espresso_machine.c, main.c]
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2023-03-12 Updated some type errors.
    [flow_meter.c]
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2023-03-16 Moved PID bias setter to its own function
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2023-03-18 Minor bugs in binary_input squashed
    [binary_input.c]
2023-03-24 Fixed casting bug in slow_pwm
    [slow_pwm.c]
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2023-03-29 Fixed bugs uncovered by -Wall and -Wextra
    [gpio_irq_timestamp.c, mb85_fram.c, nau7802.c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]
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2023-03-30 Added step files of mounts, dial, and scale
    [espresso_scale.step, led_board_mount.step, main_board_mount.step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]
2023-04-01 Squashed critical error in slow_pwm
    [slow_pwm.c]
2023-04-05 Updated MB85 api and squashed a few bugs
    [espresso_machine.c, mb85_fram.c]
2023-04-06 Small bug in MB85 library
    [mb85_fram.c]
2023-04-07 Refactored ulka_pump. Hacked in 9.5bar pressure cap for testing
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2023-04-18 Bugfix: When pump was at 100, index was out of range
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2023-04-22 Improved main loop timing to avoid compound errors
    [main.c]
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2023-05-03 Removed e-stop loop and replaced with checks in boiler/pump funs
    [espresso_machine.c, raspberry_latte_config.h]
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2023-05-21 Fixed some unit errors and added leg to machine state
    [espresso_machine.c]
2023-05-21 Shifted power for pressure by 1 to round up when cast to int
2023-06-20 PID now resets integral when setpoint changes
2023-06-20 Improved docs. Code is broken and messy right now :(
    [espresso_machine.c]
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2023-07-01 Corrected a unit error
    [espresso_machine.c]
2023-07-01 Fixed some unit errors.
    [raspberry_latte_config.h]
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2023-07-04 Reverted back from using milli for all settings
    [espresso_machine.c]
2023-07-05 Minor clearity and correctness updates.
    [espresso_machine.c]
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2023-07-10 Bugs, comments, and formatting fixes
    [espresso_machine.c]
2023-07-10 Lots of doxygen fixes
    [espresso_machine.c, gpio_irq_timestamp.c, gpio_multi_callback.c]
2023-07-11 Fixed two unit errors
    [espresso_machine.c]
2023-07-11 Fixed a few UI and unit bugs
    [espresso_machine.c]
2023-07-11 Reworked boiler preprocessor flag to fix compile error
    [espresso_machine.c]
2023-07-12 Replaced dynamic alloc with static arr in flow_meter
    [flow_meter.c]
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
